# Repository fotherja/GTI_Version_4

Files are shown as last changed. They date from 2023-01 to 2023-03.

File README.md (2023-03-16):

# GTI_Version_4
This repo contains the hardware and software files for GTIv4. This is being superseded by GTIv5 (https://github.com/fotherja/Grid_Tie_Inverter_V5)

Hardware:
KiCad was used to design the 4-Layer PCB. This was manufactured by <a href="https://www.pcbway.com/">PCBWay</a> (They produce good quality PCBs for competitive prices with excellent turnaround times).

The board uses gallium nitride MASTERGAN2s and an isolated driver chip. Four AMC1306 isolated current shunt modulators read the various analogue signals and an STM32L475 powers the board.    

Problems: 1) The EMC filter capacitors are incorrectly connected up. It may reduce the performance of the EMI filtering. 2) On testing, at about 300 Watts one of the MASTERGAN2s exploded. The exact reason is unclear and so this hardware has been redesigned into V5.

Software:
Software was developed in STM32CubeIDE. We got as far as implementing a PR controller which was extremely working well. Needs lots more work though.

Problems: I did not manage to get the DFSDM analogue watchdog feature working to provide protection in case of overcurrent or overvoltage. I asked the question on StackOverflow but got no answers (https://stackoverflow.com/questions/75287992/cant-get-the-analogue-watchdog-to-trigger-an-interrupt-on-the-dfsdm-peripheral)

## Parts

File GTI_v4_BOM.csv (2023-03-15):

Ref | Qnty | Value | Footprint | Link to Part
C1, C2, C3, C4, C10, C18, C19, C35, C39, C42, C43, C45, C48, C51, C52, C57, C60, C62, C63, C65, C68, C69, C70, | 23 | 100nF | Capacitor_SMD:C_0603_1608Metric
C5, C21, | 2 | 0.47uF | Capacitor_SMD:C_2225_5664Metric
C6, C14, C23, C26, C32, | 5 | 47nF | Capacitor_SMD:C_0402_1005Metric
C7, C8, C24, C38, C41, C47, C56, C59, C64, C67, C71, | 11 | 1uF | Capacitor_SMD:C_0603_1608Metric
C9, | 1 | 47uF | Capacitor_SMD:C_0402_1005Metric
C11, C25, C29, | 3 | 4.7uF | Capacitor_SMD:C_0603_1608Metric
C12, C13, C30, C31, | 4 | 22pF | Capacitor_SMD:C_0603_1608Metric
C15, C33, | 2 | 330pF | Capacitor_SMD:C_0603_1608Metric
C16, C17, | 2 | 20pF | Capacitor_SMD:C_0603_1608Metric
C20, | 1 | 1uF | Capacitor_THT:C_Rect_L27.0mm_W11.0mm_P22.00mm | https://www.digikey.co.uk/en/products/detail/epcos-tdk-electronics/B32672Z4105K000/1648137?so=79236903
C22, C27, C28, | 3 | 2200pF | C901U222MZVDBA7317:C901U222MZVDBA7317 | https://www.mouser.co.uk/ProductDetail/KEMET/C901U222MZVDBA7317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
C34, C49, C50, | 3 | 22uF | 595D226X9020:CAPPC3328X220N | https://www.mouser.co.uk/ProductDetail/Vishay-Sprague/595D226X9020B2T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
C36, C53, C61, | 3 | 100pF | Capacitor_SMD:C_0603_1608Metric
C37, C54, C55, | 3 | 2.2uF | Capacitor_SMD:C_0603_1608Metric
C40, C46, C58, C66, | 4 | 10nF | Capacitor_SMD:C_0603_1608Metric
C44, | 1 | 0.47uF | Capacitor_THT:C_Rect_L31.5mm_W17.0mm_P27.50mm_MKS4 | https://www.mouser.co.uk/ProductDetail/Vishay-Roederstein/MKP1848610454K2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
C73, | 1 | 10uF | Capacitor_SMD:C_0805_2012Metric
C74, C75, | 2 | 10uF | Capacitor_SMD:C_0603_1608Metric
D1, D2, D3, | 3 | SB05W05C-TB-E | SB05W05C:SOT95P250X135-3N | https://www.mouser.co.uk/ProductDetail/onsemi/SB05W05C-TB-E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
D4, | 1 | LED | LED_SMD:LED_0603_1608Metric
D6, | 1 | DIODE | ES1J:DIOM5227X250N
H1, H2, H3, H4, | 4 | MountingHole | MountingHole:MountingHole_3.2mm_M3
IC1, IC2, | 2 | MASTERGAN2TR | MASTERGAN2:MASTERGAN2TR | https://www.mouser.co.uk/ProductDetail/STMicroelectronics/MASTERGAN2TR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
IC3, IC7, IC8, | 3 | MAX253CSA+ | MAX253CSA:SOIC127P600X175-8N | https://www.mouser.co.uk/ProductDetail/Maxim-Integrated/MAX253CSA+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
IC4, IC5, IC6, IC9, | 4 | AMC1306M25QDWVRQ1 | AMC1306:SOIC127P1150X280-8N | https://www.mouser.co.uk/ProductDetail/Texas-Instruments/AMC1306M25QDWVRQ1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
J1, | 1 | Screw_Terminal_01x03 | TerminalBlock:TerminalBlock_bornier-3_P5.08mm
J2, J3, | 2 | Screw_Terminal_01x02 | TerminalBlock:TerminalBlock_bornier-2_P5.08mm
J4, | 1 | Conn_01x06_Male | Connector_PinHeader_1.27mm:PinHeader_1x06_P1.27mm_Vertical
JP1, | 1 | SolderJumper_3_Open | Jumper:SolderJumper-3_P1.3mm_Open_RoundedPad1.0x1.5mm
K1, K2, | 2 | G5LE-1 | Relay_THT:Relay_SPDT_Omron-G5LE-1 | https://www.mouser.co.uk/ProductDetail/Omron-Electronics/G5LE-1-VD-DC12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
L1, | 1 | 2mH | Inductor_THT:L_Toroid_Vertical_L35.1mm_W21.1mm_P18.50mm_Vishay_TJ6
L2, L4, | 2 | 470uH | Inductor_THT:L_Toroid_Vertical_L41.9mm_W19.1mm_P15.80mm_Vishay_TJ7
L3, | 1 | 744822301 | 744822301:WE-CMB_S5 | https://www.mouser.co.uk/ProductDetail/Wurth-Elektronik/744822301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
PS1, PS2, PS3, | 3 | AP2210K-5.0TRG1 | AP2210K-5.0TRG1:SOT95P282X130-5N | https://www.mouser.co.uk/ProductDetail/Diodes-Incorporated/AP2210K-5.0TRG1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
Q2, | 1 | 2N7002 | Package_TO_SOT_SMD:SOT-23
R1, R6, R16, R17, R18, R19, R21, R22, R23, R28, | 10 | 10R | Resistor_SMD:R_0603_1608Metric
R2, R4, R11, R15, | 4 | 47R | Resistor_SMD:R_0603_1608Metric
R3, R12, R13, R20, R27, R29, R30, | 7 | 1K | Resistor_SMD:R_0603_1608Metric
R5, R8, R9, R24, R25, R26, | 6 | 470K | Resistor_SMD:R_0805_2012Metric
R7, | 1 | 6.8R | Resistor_SMD:R_2512_6332Metric | https://www.digikey.co.uk/en/products/detail/yageo/AC2512FK-076R8L/5899890?so=79236903
R10, R14, | 2 | 50mR | Resistor_SMD:R_2512_6332Metric
T1, T2, T3, | 3 | 760390014 | 760390014:760390015 | https://www.mouser.co.uk/ProductDetail/Wurth-Elektronik/760390014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
U1, | 1 | STM32L475RCTx | Package_QFP:LQFP-64_10x10mm_P0.5mm | https://www.mouser.co.uk/ProductDetail/STMicroelectronics/STM32L475RCT3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
U2, | 1 | Si8640EC-B-IS1 | Package_SO:SOIC-16_3.9x9.9mm_P1.27mm | https://www.digikey.co.uk/en/products/detail/skyworks-solutions-inc/SI8640EC-B-IS1/2623332?so=79236903
U3, | 1 | AZ1117-5.0 | AZ1117CD-5.0TRG1:AZ1117CD50TRG1 | https://www.mouser.co.uk/ProductDetail/Diodes-Incorporated/AZ1117CD-5.0TRG1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
U4, | 1 | NCP1117-3.3_SOT223 | Package_TO_SOT_SMD:SOT-223-3_TabPin2
Y1, | 1 | ABM10-16.000MHZ-D30-T3 | Crystal:Crystal_SMD_Abracon_ABM10-4Pin_2.5x2.0mm | https://www.mouser.co.uk/ProductDetail/ABRACON/ABM10-16.000MHZ-D30-T3?qs=yJy3i4hRrMhOYZI5v9%2F5mA%3D%3D

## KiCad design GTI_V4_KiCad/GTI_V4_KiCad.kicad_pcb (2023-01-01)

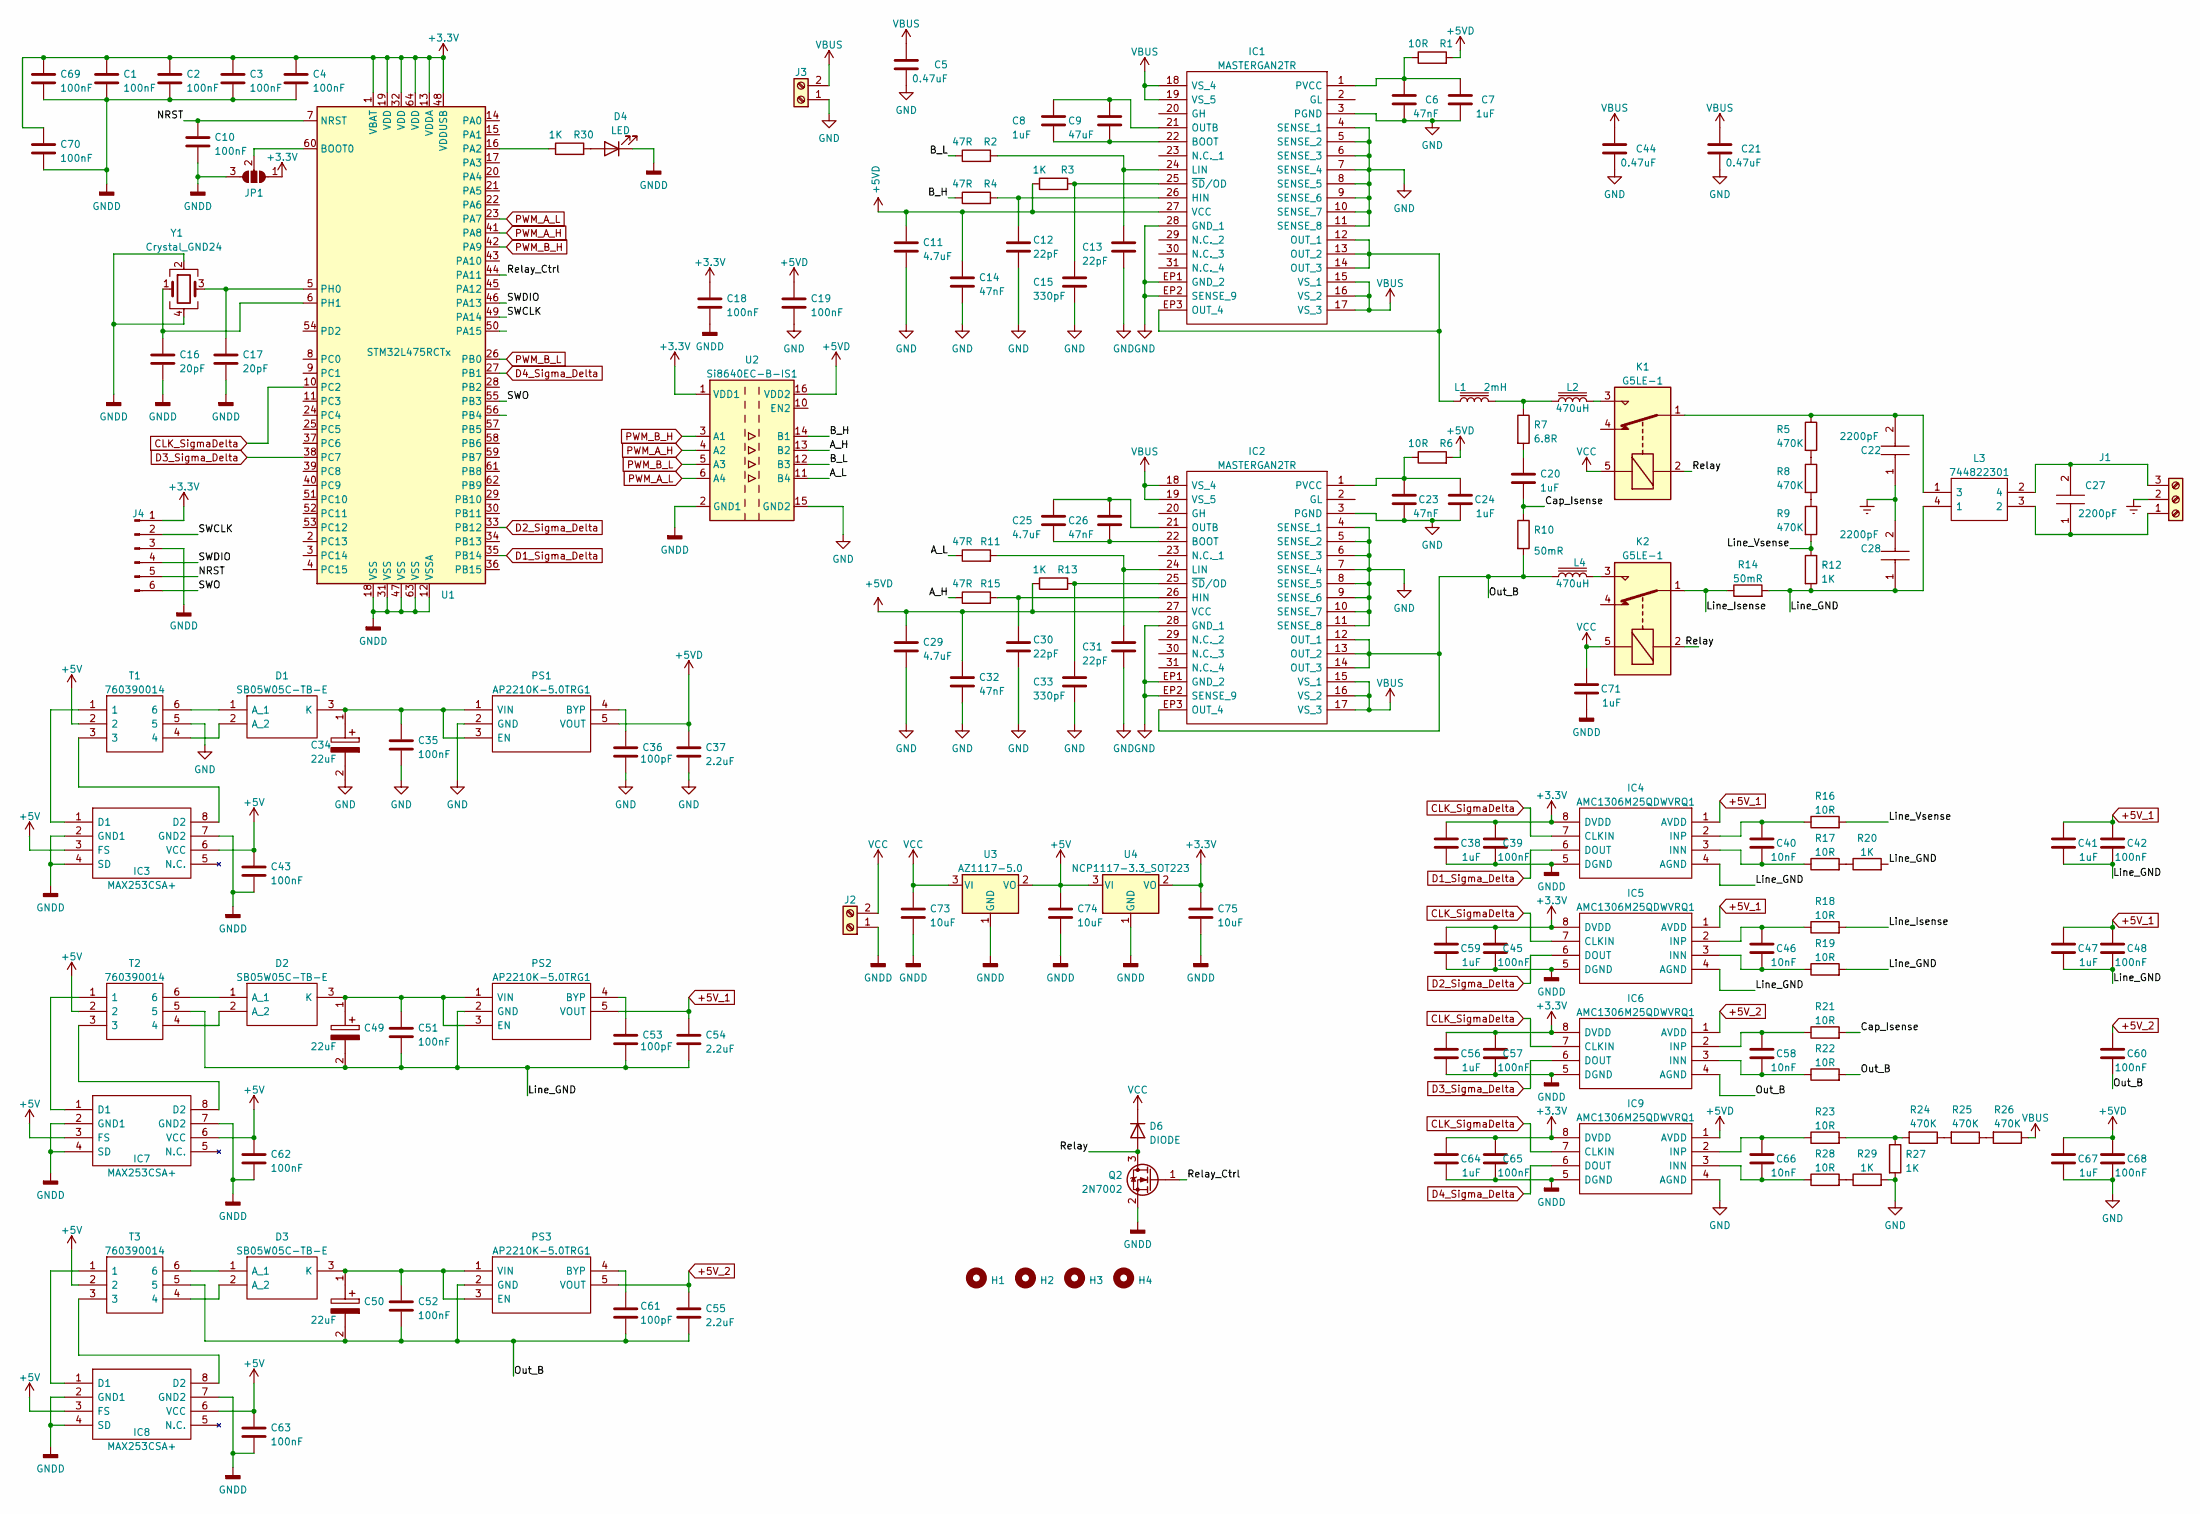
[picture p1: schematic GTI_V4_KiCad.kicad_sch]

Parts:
C1, C2, C3, C4, C10, C18, C19, C35, C39, C42, C43, C45, C48, C51, C52, C57, C60, C62, C63, C65, C68, C69, C70: 100nF; C_0603_1608Metric
C5, C21: 0.47uF; C_2225_5664Metric
C6, C14, C23, C26, C32: 47nF; C_0402_1005Metric
C7, C8, C24, C38, C41, C47, C56, C59, C64, C67, C71: 1uF; C_0603_1608Metric
C9: 47uF; C_0402_1005Metric
C11, C25, C29: 4.7uF; C_0603_1608Metric
C12, C13, C30, C31: 22pF; C_0603_1608Metric
C15, C33: 330pF; C_0603_1608Metric
C16, C17: 20pF; C_0603_1608Metric
C20: 1uF; C_Rect_L27.0mm_W11.0mm_P22.00mm
C22, C27, C28: 2200pF; C901U222MZVDBA7317; Mouser Part Number 80-C901U222MZVDBAP
C34, C49, C50: 22uF; CAPPC3328X220N; Mouser Part Number 74-595D226X9020B2T
C36, C53, C61: 100pF; C_0603_1608Metric
C37, C54, C55: 2.2uF; C_0603_1608Metric
C40, C46, C58, C66: 10nF; C_0603_1608Metric
C44: 0.47uF; C_Rect_L31.5mm_W17.0mm_P27.50mm_MKS4
C73: 10uF; C_0805_2012Metric
C74, C75: 10uF; C_0603_1608Metric
D1, D2, D3: SB05W05C-TB-E; SOT95P250X135-3N; Mouser Part Number 863-SB05W05C-TB-E
D4: LED; LED_0603_1608Metric
D6: DIODE; DIOM5227X250N
H1, H2, H3, H4: MountingHole; MountingHole_3.2mm_M3
IC1, IC2: MASTERGAN2TR; Mouser Part Number 511-MASTERGAN2TR
IC3, IC7, IC8: MAX253CSA+; SOIC127P600X175-8N; Mouser Part Number 700-MAX253CSA
IC4, IC5, IC6, IC9: AMC1306M25QDWVRQ1; SOIC127P1150X280-8N; Mouser Part Number 595-MC1306M25QDWVRQ1
J1: Screw_Terminal_01x03; TerminalBlock_bornier-3_P5.08mm
J2, J3: Screw_Terminal_01x02; TerminalBlock_bornier-2_P5.08mm
J4: Conn_01x06_Male; PinHeader_1x06_P1.27mm_Vertical
JP1: SolderJumper_3_Open; SolderJumper-3_P1.3mm_Open_RoundedPad1.0x1.5mm
K1, K2: G5LE-1; Relay_SPDT_Omron-G5LE-1
L1: 2mH; L_Toroid_Vertical_L35.1mm_W21.1mm_P18.50mm_Vishay_TJ6
L2, L4: 470uH; L_Toroid_Vertical_L41.9mm_W19.1mm_P15.80mm_Vishay_TJ7
L3: 744822301; WE-CMB_S5; Mouser Part Number 710-744822301
PS1, PS2, PS3: AP2210K-5.0TRG1; SOT95P282X130-5N; Mouser Part Number 621-AP2210K-5.0TRG1
Q2: 2N7002; SOT-23
R1, R6, R16, R17, R18, R19, R21, R22, R23, R28: 10R; R_0603_1608Metric
R2, R4, R11, R15: 47R; R_0603_1608Metric
R3, R12, R13, R20, R27, R29, R30: 1K; R_0603_1608Metric
R5, R8, R9, R24, R25, R26: 470K; R_0805_2012Metric
R7: 6.8R; R_2512_6332Metric
R10, R14: 50mR; R_2512_6332Metric
T1, T2, T3: 760390014; 760390015; Mouser Part Number 710-760390014
U1: STM32L475RCTx; LQFP-64_10x10mm_P0.5mm
U2: Si8640EC-B-IS1; SOIC-16_3.9x9.9mm_P1.27mm
U3: AZ1117-5.0; AZ1117CD50TRG1
U4: NCP1117-3.3_SOT223; SOT-223-3_TabPin2
Y1: Crystal_GND24; Crystal_SMD_Abracon_ABM10-4Pin_2.5x2.0mm

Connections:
+3.3V: C1.1, C2.1, C3.1, C4.1, C18.1, C38.1, C39.1, C45.1, C56.1, C57.1, C59.1, C64.1, C65.1, C69.1, C70.1, C75.1, IC4.8 (DVDD), IC5.8 (DVDD), IC6.8 (DVDD), IC9.8 (DVDD), J4.1, JP1.1 (A), U1.1 (VBAT), U1.13 (VDDA), U1.19 (VDD), U1.32 (VDD), U1.48 (VDDUSB), U1.64 (VDD), U2.1 (VDD1), U4.2 (VO)
+5V: C43.1, C62.1, C63.1, C74.1, IC3.3 (FS), IC3.6 (VCC), IC7.3 (FS), IC7.6 (VCC), IC8.3 (FS), IC8.6 (VCC), T1.2, T2.2, T3.2, U3.2 (VO), U4.3 (VI)
+5VD: C11.1, C14.1, C19.1, C29.1, C32.1, C37.1, C67.1, C68.1, IC1.27 (VCC), IC2.27 (VCC), IC9.1 (AVDD), PS1.5 (VOUT), R1.2, R3.1, R6.2, R13.1, U2.16 (VDD2)
+5V_1: C41.1, C42.1, C47.1, C48.1, C54.1, IC4.1 (AVDD), IC5.1 (AVDD), PS2.5 (VOUT)
+5V_2: C55.1, C60.1, IC6.1 (AVDD), PS3.5 (VOUT)
/A_H: R15.1, U2.13 (B2)
/A_L: R11.1, U2.11 (B4)
/B_H: R4.1, U2.14 (B1)
/B_L: R2.1, U2.12 (B3)
/Cap_Isense: C20.2, R10.1, R21.2
/Line_GND: C28.1, C41.2, C42.2, C47.2, C48.2, C49.2, C51.2, C53.2, C54.2, IC4.4 (AGND), IC5.4 (AGND), L3.4 (1), PS2.2 (GND), R12.2, R14.2, R19.2, R20.2, T2.5
/Line_Isense: K2.1, R14.1, R18.2
/Line_Vsense: R9.2, R12.1, R16.2
/NRST: C10.1, J4.5, U1.7 (NRST)
/Out_B: C50.2, C52.2, C55.2, C60.2, C61.2, IC2.12 (OUT_1), IC2.13 (OUT_2), IC2.14 (OUT_3), IC2.EP3 (OUT_4), IC6.4 (AGND), L4.1, PS3.2 (GND), R10.2, R22.2, T3.5
/Relay: D6.1 (A), K1.2, K2.2, Q2.3 (D)
/Relay_Ctrl: Q2.1 (G), U1.44 (PA11)
/SWCLK: J4.2, U1.49 (PA14)
/SWDIO: J4.4, U1.46 (PA13)
/SWO: J4.6, U1.55 (PB3)
CLK_SigmaDelta: IC4.7 (CLKIN), IC5.7 (CLKIN), IC6.7 (CLKIN), IC9.7 (CLKIN), U1.10 (PC2)
D1_Sigma_Delta: IC4.6 (DOUT), U1.35 (PB14)
D2_Sigma_Delta: IC5.6 (DOUT), U1.33 (PB12)
D3_Sigma_Delta: IC6.6 (DOUT), U1.38 (PC7)
D4_Sigma_Delta: IC9.6 (DOUT), U1.27 (PB1)
Earth: C22.1, C28.2, J1.2
GND: C5.2, C6.2, C7.2, C11.2, C12.2, C13.2, C14.2, C15.2, C19.2, C21.2, C23.2, C24.2, C29.2, C30.2, C31.2, C32.2, C33.2, C34.2, C35.2, C36.2, C37.2, C44.2, C67.2, C68.2, IC1.3 (PGND), IC1.4 (SENSE_1), IC1.5 (SENSE_2), IC1.6 (SENSE_3), IC1.7 (SENSE_4), IC1.8 (SENSE_5), IC1.9 (SENSE_6), IC1.10 (SENSE_7), IC1.11 (SENSE_8), IC1.28 (GND_1), IC1.EP1 (GND_2), IC1.EP2 (SENSE_9), IC2.3 (PGND), IC2.4 (SENSE_1), IC2.5 (SENSE_2), IC2.6 (SENSE_3), IC2.7 (SENSE_4), IC2.8 (SENSE_5), IC2.9 (SENSE_6), IC2.10 (SENSE_7), IC2.11 (SENSE_8), IC2.28 (GND_1), IC2.EP1 (GND_2), IC2.EP2 (SENSE_9), IC9.4 (AGND), J3.1, PS1.2 (GND), R27.2, R29.2, T1.5, U2.9 (GND2), U2.15 (GND2)
GNDD: C1.2, C2.2, C3.2, C4.2, C10.2, C16.2, C17.2, C18.2, C38.2, C39.2, C43.2, C45.2, C56.2, C57.2, C59.2, C62.2, C63.2, C64.2, C65.2, C69.2, C70.2, C71.2, C73.2, C74.2, C75.2, D4.1 (K), IC3.2 (GND1), IC3.4 (SD), IC3.7 (GND2), IC4.5 (DGND), IC5.5 (DGND), IC6.5 (DGND), IC7.2 (GND1), IC7.4 (SD), IC7.7 (GND2), IC8.2 (GND1), IC8.4 (SD), IC8.7 (GND2), IC9.5 (DGND), J2.1, J4.3, JP1.3 (B), Q2.2 (S), U1.12 (VSSA), U1.18 (VSS), U1.31 (VSS), U1.47 (VSS), U1.63 (VSS), U2.2 (GND1), U2.8 (GND1), U3.1 (GND), U4.1 (GND), Y1.2, Y1.4
unnamed: C6.1, C7.1, IC1.1 (PVCC), R1.1
unnamed: C8.1, C9.1, IC1.21 (OUTB)
unnamed: C8.2, C9.2, IC1.22 (BOOT)
unnamed: C12.1, IC1.26 (HIN), R4.2
unnamed: C13.1, IC1.24 (LIN), R2.2
unnamed: C15.1, IC1.25 (~SD/OD), R3.2
unnamed: C16.1, U1.6 (PH1), Y1.1
unnamed: C17.1, U1.5 (PH0), Y1.3
unnamed: C20.1, R7.2
unnamed: C22.2, K1.1, L3.1 (3), R5.1
unnamed: C23.1, C24.1, IC2.1 (PVCC), R6.1
unnamed: C25.1, C26.1, IC2.21 (OUTB)
unnamed: C25.2, C26.2, IC2.22 (BOOT)
unnamed: C27.1, J1.1, L3.3 (2)
unnamed: C27.2, J1.3, L3.2 (4)
unnamed: C30.1, IC2.26 (HIN), R15.2
unnamed: C31.1, IC2.24 (LIN), R11.2
unnamed: C33.1, IC2.25 (~SD/OD), R13.2
unnamed: C34.1, C35.1, D1.3 (K), PS1.1 (VIN), PS1.3 (EN)
unnamed: C36.1, PS1.4 (BYP)
unnamed: C40.1, IC4.2 (INP), R16.1
unnamed: C40.2, IC4.3 (INN), R17.1
unnamed: C46.1, IC5.2 (INP), R18.1
unnamed: C46.2, IC5.3 (INN), R19.1
unnamed: C49.1, C51.1, D2.3 (K), PS2.1 (VIN), PS2.3 (EN)
unnamed: C50.1, C52.1, D3.3 (K), PS3.1 (VIN), PS3.3 (EN)
unnamed: C53.1, PS2.4 (BYP)
unnamed: C58.1, IC6.2 (INP), R21.1
unnamed: C58.2, IC6.3 (INN), R22.1
unnamed: C61.1, PS3.4 (BYP)
unnamed: C66.1, IC9.2 (INP), R23.1
unnamed: C66.2, IC9.3 (INN), R28.1
unnamed: D1.1 (A_1), T1.6
unnamed: D1.2 (A_2), T1.4
unnamed: D2.1 (A_1), T2.6
unnamed: D2.2 (A_2), T2.4
unnamed: D3.1 (A_1), T3.6
unnamed: D3.2 (A_2), T3.4
unnamed: D4.2 (A), R30.2
unnamed: IC1.12 (OUT_1), IC1.13 (OUT_2), IC1.14 (OUT_3), IC1.EP3 (OUT_4), L1.1
unnamed: IC3.1 (D1), T1.1
unnamed: IC3.8 (D2), T1.3
unnamed: IC7.1 (D1), T2.1
unnamed: IC7.8 (D2), T2.3
unnamed: IC8.1 (D1), T3.1
unnamed: IC8.8 (D2), T3.3
unnamed: JP1.2 (C), U1.60 (BOOT0)
unnamed: K1.3, L2.2
unnamed: K2.3, L4.2
unnamed: L1.2, L2.1, R7.1
unnamed: R5.2, R8.1
unnamed: R8.2, R9.1
unnamed: R17.2, R20.1
unnamed: R23.2, R24.2, R27.1
unnamed: R24.1, R25.2
unnamed: R25.1, R26.2
unnamed: R28.2, R29.1
unnamed: R30.1, U1.16 (PA2)
PWM_A_H: U1.41 (PA8), U2.4 (A2)
PWM_A_L: U1.23 (PA7), U2.6 (A4)
PWM_B_H: U1.42 (PA9), U2.3 (A1)
PWM_B_L: U1.26 (PB0), U2.5 (A3)
VBUS: C5.1, C21.1, C44.1, IC1.15 (VS_1), IC1.16 (VS_2), IC1.17 (VS_3), IC1.18 (VS_4), IC1.19 (VS_5), IC2.15 (VS_1), IC2.16 (VS_2), IC2.17 (VS_3), IC2.18 (VS_4), IC2.19 (VS_5), J3.2, R26.1
VCC: C71.1, C73.1, D6.2 (K), J2.2, K1.5, K2.5, U3.3 (VI)

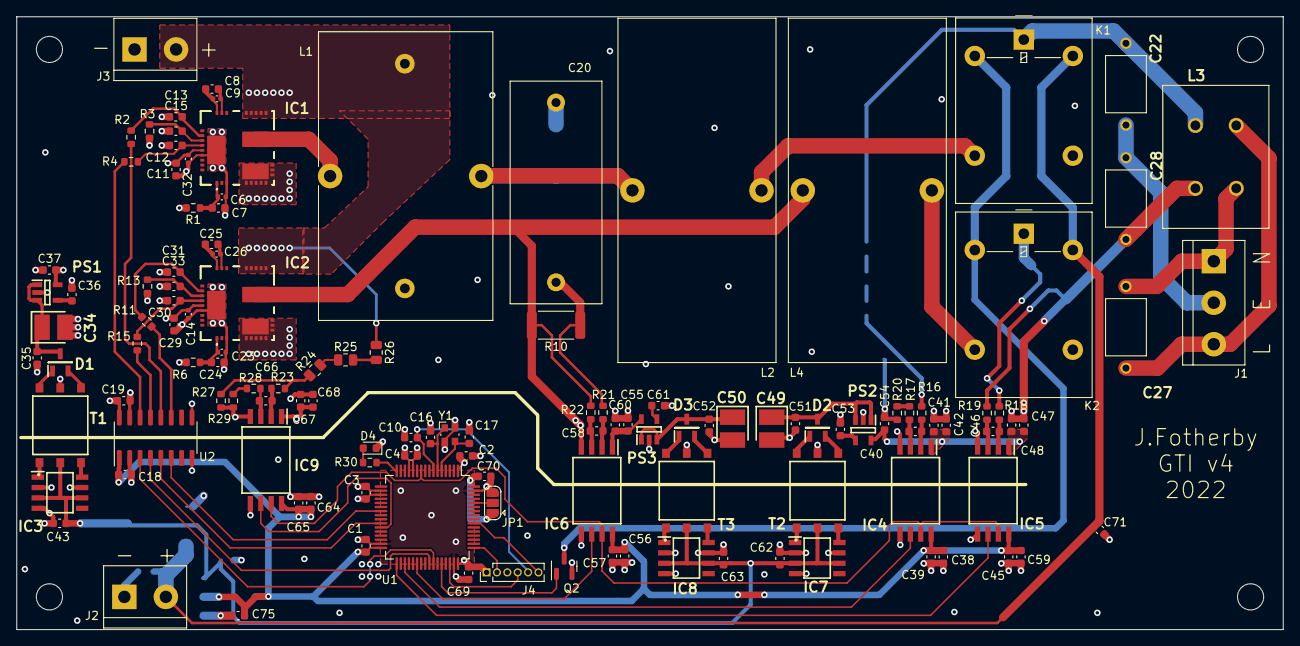
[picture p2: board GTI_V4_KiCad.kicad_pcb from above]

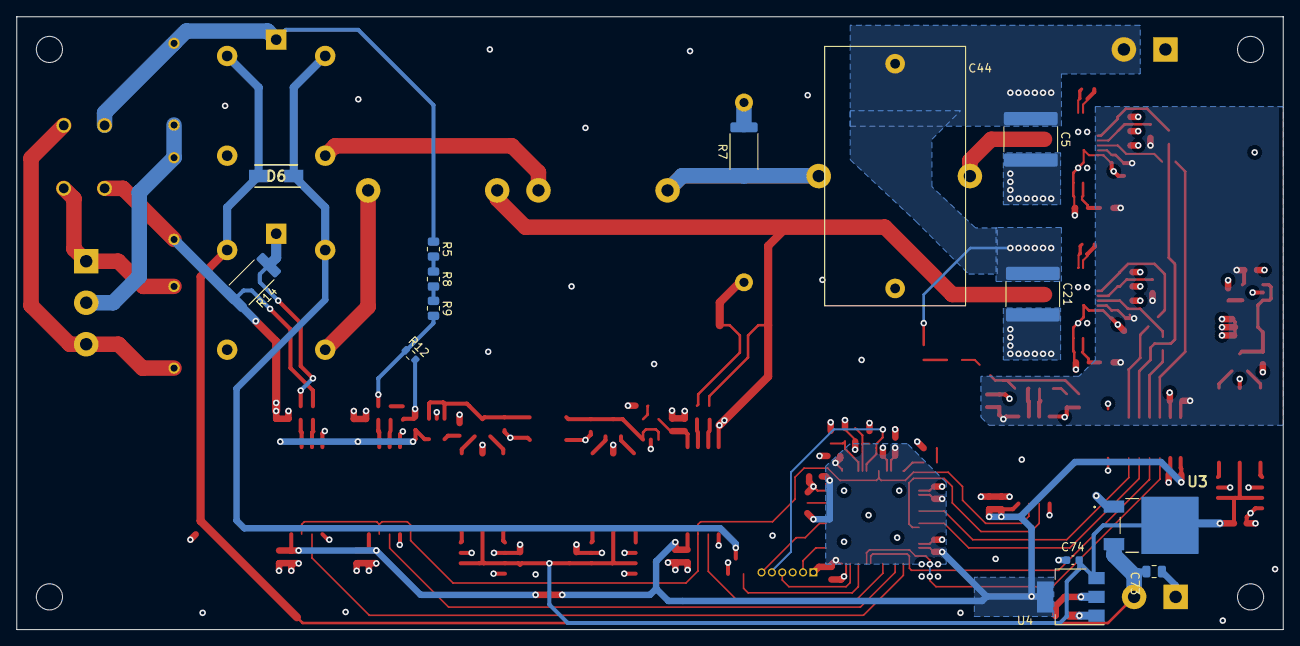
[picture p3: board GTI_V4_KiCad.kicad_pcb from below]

Board: 4 copper layers, 155.0 x 75.0 mm, 145 parts (14 on the bottom side), 92 nets.

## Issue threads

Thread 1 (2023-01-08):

Hi

Jmenotts, 2023-01-08:
My name is James i'm new to this and ive downloaded your files but cant seem to get the code for the stm32 chip but isnt in the download folder? also will this work on an esp32 by any chance i'm trying to build a grid tie inverter so i can save some electric thanks in advance buddy.

fotherja, 2023-01-08:
Hi, GTI_Version 4 is a work in progress. In this repo are just the PCB design files atm. I'm waiting for the PCB board to be posted (due 10th Jan).
Once I receive the PCB I need to assemble it and adapt/improve the software.
With version 4 I want to implement a PR controller.

Jmenotts, 2023-01-08:
Hi and thank you for your email buddy your work is incredible tbh and I'm
following extensively do you have working code I can play with on any
version you have? I'm dying to get into this field and have a play with
this renewable energy stuff it's very intriguing. Thanks in advance

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

fotherja, 2023-01-08:
Thanks. I think the code I've been using for the previous versions needs a total overhaul. Here are some useful resources:
Poldo on instructables: https://www.instructables.com/search/projects/?q=poldo&projects=all
PR controllers and how to implement them: https://imperix.com/doc/implementation/proportional-resonant-controller

Watch this space. Hope in the next month to get version 4 made.

Jmenotts, 2023-01-08:
Awesome, thanks! Will look forward to the update buddy

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

Flole998, 2023-02-09:
I'm also looking into building a grid tie inverter. At this point I am doing hardware design since I am trying to avoid using transformers. I'm trying to use a charge pump  for step-up conversion and I will shortly have the first revision of my PCB produced. Since the H-Bridge and filters are similar in our designs I believe we can learn a lot from each other when it comes to the software.

fotherja, 2023-02-15:
Hi,
I'm very interested to hear more. How are you planning to use a charge pump
for hundreds of watts? Can I see your PCB designs?

I'm writing up my 4th attempt and will post it soon. I have managed to
implement a PR controller very well. I was very pleased with my hardware
for my 4th attempt. Everything was going extremely well until a MOSFET
package blew up a couple days ago... So now I think I need to look into a
5th version and some hardware changes.

Yes I'd be very keen to collaborate with the code. What microprocessor are
you using? Stay in touch. my email is ***@***.***

James

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

Flole998, 2023-02-15:
Hi James,

unfortunately GitHub censored your email address :D

My idea is to use the design from https://onlinelibrary.wiley.com/cms/asset/b8836dac-32ef-46b6-ad67-28f952f7738e/etep12622-toc-0001-m.jpg which was tested at 150W and converted 18V into 350V, as it's basically doing multiplication of the input voltage at 36V I could already get 700V out of it if I'm not mistaken, increasing the current should pull the voltage down and also increase output power.

I'm using an Attiny3226 for the boost converter (and MPTT, measuring input voltage and current) and an AVR128DB32 for the H bridge, measuring zero cross, output voltage and current and communication with a CAN bus (I use that for my building automation).

fotherja, 2023-02-21:
Hey,

Interesting. Well keep me updated with your progress. I have a gmail
address. And prior to the @ sign is the same as my github username...

I have just posted my version 4 attempt.
https://www.instructables.com/Grid-Tie-Inverter-V4/

James

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

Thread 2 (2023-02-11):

CT Current limiting

folny, 2023-02-11:
Hi

I like your project and I'm already very curious about the first tests, I want to ask if in the future you plan to add an input for the CT sensor to the project to prevent the flow of current into the distributor network.

https://www.aliexpress.com/item/1005004501300085.html

fotherja, 2023-02-15:
Hi,
Thanks. I'm writing up my 4th attempt and will post it soon. Unfortunately,
I'll need a 5th attempt. The 4th version was going extremely well until it
blew up...
Yes, a CT sensor will be very useful in future.
James

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

folny, 2023-02-17:
I'm keeping my fingers crossed and I'll be watching your project and I hope you'll soon figure out how to bring it to perfection :-)

fotherja, 2023-02-21:
Hey,

I have just posted my version 4 attempt.
https://www.instructables.com/Grid-Tie-Inverter-V4/

Already thinking about version 5. If you have any recommendations, I'd be
glad to hear them.

James

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

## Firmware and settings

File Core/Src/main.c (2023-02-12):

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
/* Includes ------------------------------------------------------------------*/
#include "main.h"
#include "dac.h"
#include "dfsdm.h"
#include "dma.h"
#include "tim.h"
#include "gpio.h"

/* USER CODE BEGIN Includes */
#include "PID.h"
#include "math.h"
/* USER CODE END Includes */


/* USER CODE BEGIN PV */
float Sin_LookupF[65] =
{
		0, 25.09238792, 49.94312244, 74.31287738, 97.96695869, 120.6775646, 142.2259797, 162.4046807,
		181.019336, 197.8906761, 212.8562207, 225.7718437, 236.5131603, 244.9767259, 251.0810318, 254.76729,
		256, 254.76729, 251.0810318, 244.9767259, 236.5131603, 225.7718437, 212.8562207, 197.8906761,
		181.019336,	162.4046807, 142.2259797, 120.6775646, 97.96695869, 74.31287738, 49.94312244, 25.09238792,
		0, -25.09238792, -49.94312244, -74.31287738, -97.96695869, -120.6775646, -142.2259797, -162.4046807,
		-181.019336, -197.8906761, -212.8562207, -225.7718437, -236.5131603, -244.9767259, -251.0810318, -254.76729,
		-256, -254.76729, -251.0810318, -244.9767259, -236.5131603, -225.7718437, -212.8562207, -197.8906761,
		-181.019336, -162.4046807, -142.2259797, -120.6775646, -97.96695869, -74.31287738, -49.94312244, -25.09238792,
		0
};

float Cos_LookupF[65] =
{
		256, 254.76729, 251.0810318, 244.9767259, 236.5131603, 225.7718437, 212.8562207, 197.8906761,
		181.019336, 162.4046807, 142.2259797, 120.6775646, 97.96695869, 74.31287738, 49.94312244, 25.09238792,
		0, -25.09238792, -49.94312244, -74.31287738, -97.96695869, -120.6775646, -142.2259797, -162.4046807,
		-181.019336, -197.8906761, -212.8562207, -225.7718437, -236.5131603, -244.9767259, -251.0810318, -254.76729,
		-256, -254.76729, -251.0810318, -244.9767259, -236.5131603, -225.7718437, -212.8562207, -197.8906761,
		-181.019336, -162.4046807, -142.2259797, -120.6775646, -97.96695869, -74.31287738, -49.94312244, -25.09238792,
		0, 25.09238792, 49.94312244, 74.31287738, 97.96695869, 120.6775646, 142.2259797, 162.4046807,
		181.019336,	197.8906761, 212.8562207, 225.7718437, 236.5131603, 244.9767259, 251.0810318, 254.76729,
		256
};

// PID Structures
PIDControl 			PLL_PID, I_OUT_PID; 										// These structures are used to store the respective PID variables

// DMA buffers and flags
int32_t 			Vbus_DMA[1], Igrid_DMA[1], Vgrid_DMA[1], Icap_DMA[1];
uint32_t			Channel_1_DUTY[1], Channel_2_DUTY[1];

// Voltage and Current values
float 				I_grid, V_grid, I_cap, V_bus; 								// These are our SI unit values

// LO Phase
uint8_t 			_50_Index = 0;

volatile uint8_t 	Error_Code;
volatile float 		I_Output_Demand = 0;

volatile uint8_t    Run_Controller_Flag = 0;
volatile uint8_t	Run_Grid_Checks_Flag = 0;
volatile uint8_t	Run_PLL_Flag = 0;
uint8_t				HB_Enabled_Flag = false;

/* USER CODE END PV */

void SystemClock_Config(void);
/* USER CODE BEGIN PFP */
void HB_Disable(void);
void HB_Enable(void);
float Integral(int32_t datum);
void Grid_Checks(void);
void Controller(void);
void PLL(void);
void Main_Loop(void);
int32_t Integrate_Mains_MS(int32_t grid_voltage_sample);
void HAL_DFSDM_FilterAwdCallback(DFSDM_Filter_HandleTypeDef *hdfsdm_filter, uint32_t Channel, uint32_t Threshold);
void HAL_DFSDM_FilterRegConvCpltCallback(DFSDM_Filter_HandleTypeDef *hdfsdm_filter);
/* USER CODE END PFP */

/**
  * @brief  The application entry point.
  * @retval int
  */
int main(void)
{
  /* MCU Configuration--------------------------------------------------------*/

  /* Reset of all peripherals, Initializes the Flash interface and the Systick. */
  HAL_Init();

  /* Configure the system clock */
  SystemClock_Config();

  /* Initialize all configured peripherals */
  MX_GPIO_Init();
  MX_DMA_Init();
  MX_TIM1_Init();
  MX_TIM3_Init();
  MX_DFSDM1_Init();
  MX_TIM2_Init();
  MX_TIM4_Init();
  MX_DAC1_Init();
  /* USER CODE BEGIN 2 */
  // Initialise the PID controller for the PLL
  PIDInit(&PLL_PID, PLL_Kp, PLL_Ki, PLL_Kd, PLL_PERIOD, -PLL_LIMIT, PLL_LIMIT, AUTOMATIC, DIRECT, P_ON_E);
  PIDInit(&I_OUT_PID, I_OUT_Kp, I_OUT_Ki, I_OUT_Kd, I_OUT_PERIOD, -I_OUT_Limit, I_OUT_Limit, AUTOMATIC, DIRECT, P_ON_E);

  // Initialise our timers
  HAL_TIM_Base_Start_IT(&htim2);
  HAL_TIM_Base_Start_IT(&htim3);
  HAL_TIM_Base_Start_IT(&htim4);

  // Initialise DAC and LED for Debugging
  HAL_DAC_Start(&hdac1, DAC_CHANNEL_2);
  HAL_GPIO_WritePin(GPIOA, Relay_Pin, GPIO_PIN_SET);

  // Start the DFSDMs
  HAL_DFSDM_FilterRegularStart_DMA(&hdfsdm1_filter0, Vbus_DMA, 1);
  HAL_DFSDM_FilterRegularStart_DMA(&hdfsdm1_filter1, Igrid_DMA, 1);
  HAL_DFSDM_FilterRegularStart_DMA(&hdfsdm1_filter2, Vgrid_DMA, 1);
  HAL_DFSDM_FilterRegularStart_DMA(&hdfsdm1_filter3, Icap_DMA, 1);

  // This should enable the interrupts by the analogue watchdog ----------- BUT IT DOESN'T!!!
  DFSDM_Filter_AwdParamTypeDef awdParamFilter0;
  awdParamFilter0.DataSource = DFSDM_FILTER_AWD_FILTER_DATA;
  awdParamFilter0.Channel = DFSDM_CHANNEL_0;
  awdParamFilter0.HighBreakSignal = DFSDM_NO_BREAK_SIGNAL;
  awdParamFilter0.HighThreshold = 250;
  awdParamFilter0.LowBreakSignal = DFSDM_NO_BREAK_SIGNAL;
  awdParamFilter0.LowThreshold = -250;
  HAL_DFSDM_FilterAwdStart_IT(&hdfsdm1_filter0, &awdParamFilter0);

  DFSDM_Filter_AwdParamTypeDef awdParamFilter1;
  awdParamFilter1.DataSource = DFSDM_FILTER_AWD_FILTER_DATA;
  awdParamFilter1.Channel = DFSDM_CHANNEL_1;
  awdParamFilter1.HighBreakSignal = DFSDM_NO_BREAK_SIGNAL;
  awdParamFilter1.HighThreshold = 250;
  awdParamFilter1.LowBreakSignal = DFSDM_NO_BREAK_SIGNAL;
  awdParamFilter1.LowThreshold = -250;
  HAL_DFSDM_FilterAwdStart_IT(&hdfsdm1_filter1, &awdParamFilter1);

  HAL_GPIO_WritePin(GPIOA, LED_Pin, GPIO_PIN_SET);
  /* USER CODE END 2 */

  /* Infinite loop */
  /* USER CODE BEGIN WHILE */

  while (1)
  {
    /* USER CODE END WHILE */

    /* USER CODE BEGIN 3 */
	  Main_Loop();
  }
  /* USER CODE END 3 */
}

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
/* USER CODE BEGIN 4 */
void Main_Loop()	{
	if(Run_Controller_Flag == 1)	{
		Run_Controller_Flag = 0;
		Controller();
	}

	if(Run_Grid_Checks_Flag == 1)	{
		Run_Grid_Checks_Flag = 0;
		Grid_Checks();
	}

	if(Run_PLL_Flag == 1)	{
		Run_PLL_Flag = 0;
		PLL();
	}
}

void HB_Disable() {
	// Disable the H-Bridge
	HAL_TIM_PWM_Stop(&htim1, TIM_CHANNEL_1);
	HAL_TIMEx_PWMN_Stop(&htim1, TIM_CHANNEL_1);
	HAL_TIM_PWM_Stop(&htim1, TIM_CHANNEL_2);
	HAL_TIMEx_PWMN_Stop(&htim1, TIM_CHANNEL_2);
	HB_Enabled_Flag = false;

	htim1.Instance->CCR1 = 0;
	htim1.Instance->CCR2 = 0;

	HAL_GPIO_WritePin(GPIOA, LED_Pin, GPIO_PIN_SET);
}

void HB_Enable() {
	// Start our PWM driver which uses Timer1 to power our H-bridge. Both channels start with Duty = 0
	HAL_GPIO_WritePin(GPIOA, LED_Pin, GPIO_PIN_RESET);

	HAL_TIM_PWM_Start(&htim1, TIM_CHANNEL_1);
	HAL_TIMEx_PWMN_Start(&htim1, TIM_CHANNEL_1);
	HAL_TIM_PWM_Start(&htim1, TIM_CHANNEL_2);
	HAL_TIMEx_PWMN_Start(&htim1, TIM_CHANNEL_2);
	HB_Enabled_Flag = true;
}

float Integral(int32_t datum)
{
	// Keep a running summation of the last INTEGRAL_SIZE values passed into this function.
	static int32_t 		Buffer[INTEGRAL_SIZE];
	static int16_t  	Index = 0;
	static int32_t  	Sum = 0;

	Sum += datum;

	Buffer[Index++] = datum;

	if(Index == INTEGRAL_SIZE)
		Index = 0;

	Sum -= Buffer[Index];
	return((float)Sum);
}

int32_t Integrate_Mains_MS(int32_t grid_voltage_sample)
{
	// Maintain an MS measurement of the grid voltage. Runs at 800Hz which is 16 samples per period
	static int32_t 		Buffer[RMS_INTEGRAL_SIZE];
	static int8_t  		Index = 0;
	static int32_t  	Sum = 0;

	int32_t Sample_sqrd = grid_voltage_sample * grid_voltage_sample;

	Sum += Sample_sqrd;

	Buffer[Index++] = Sample_sqrd;

	if(Index == RMS_INTEGRAL_SIZE)
		Index = 0;

	Sum -= Buffer[Index];

	int32_t Mean_Squared = Sum >> 6;			// Divide Sum by 64 (RMS_INTEGRAL_SIZE)
	return(Mean_Squared);						// return(sqrtf(RMS));
}

void HAL_DFSDM_FilterAwdCallback(DFSDM_Filter_HandleTypeDef *hdfsdm_filter, uint32_t Channel, uint32_t Threshold)
{
	// Callback if Analogue watch dog triggers ---------- BUT CAN'T GET THIS TO RUN!!!!
}

void HAL_DFSDM_FilterRegConvCpltCallback(DFSDM_Filter_HandleTypeDef *hdfsdm_filter)	{
	if(hdfsdm_filter == &hdfsdm1_filter0)	{
		V_bus = (float)Vbus_DMA[0] * 2.4414e-7 + 5.0e-4;
	}
	if(hdfsdm_filter == &hdfsdm1_filter1)	{
		I_grid = (float)Igrid_DMA[0] * -3.1738e-9 + 8.75e-6;
	}
	if(hdfsdm_filter == &hdfsdm1_filter2)	{
		V_grid = (float)Vgrid_DMA[0] * 2.4414e-7 + 5.0e-4;
	}
	if(hdfsdm_filter == &hdfsdm1_filter3)	{
		I_cap = (float)Icap_DMA[0] * 3.1738e-9 - 8.75e-6;
	}
}

void Grid_Checks()	{
	// Calculate some grid metrics for some following checks
	static int16_t 	Grid_Good_Bad_Cnt = GRID_UNACCEPTABLE;

	int32_t Mains_MS = Integrate_Mains_MS((int32_t)V_grid); 						// Update our mains RMS measurement
	float Freq_Offset = PLL_PID.output * F_CONVERSION_K; 							// Get the frequency difference between the grid and a 50Hz reference

	// These are high priority checks:
	if(V_bus > V_BUS_MAXIMUM)	{													// If our DC Bus voltage is too high cut-out immediately
		HB_Disable();
		Grid_Good_Bad_Cnt = GRID_UNACCEPTABLE;
		Error_Code |= 0b00001;
	}

	if(I_grid > I_OUTPUT_MAXIMUM || I_grid < -I_OUTPUT_MAXIMUM)	{					// Likewise, if we detect excess current flowing, cut-out immediately
		HB_Disable();
		Grid_Good_Bad_Cnt = GRID_UNACCEPTABLE;
		Error_Code |= 0b00010;
	}

	// These are lower priority checks and have to be out of range for an amount of time
	if(Mains_MS > RMS_UPPER_LIMIT || Mains_MS < RMS_LOWER_LIMIT)	{				// If mains RMS voltage whacky
		Grid_Good_Bad_Cnt -= GRID_BAD_FAIL_RATE;
		Error_Code |= 0b00100;
	}

	if(Freq_Offset > FREQ_DEVIATION_LIMIT || Freq_Offset < -FREQ_DEVIATION_LIMIT)	{
	//	Grid_Good_Bad_Cnt -= GRID_BAD_FAIL_RATE;									// If our mains frequency is out of tolerance
		Error_Code |= 0b01000;
	}

	if(V_bus < V_BUS_MINIMUM)	{													// If our DC Bus voltage is too low
		Grid_Good_Bad_Cnt -= GRID_BAD_FAIL_RATE;
		Error_Code |= 0b10000;
	}

	// Act on the above checks
	if(Grid_Good_Bad_Cnt < GRID_OK)	{												// If our metrics have been whacky for too long stop output
		if(HB_Enabled_Flag == true) {
			HB_Disable(); 															// This puts the H-bridge into a high impedance state
			Grid_Good_Bad_Cnt = GRID_UNACCEPTABLE;
		}
	}

	if(HB_Enabled_Flag == false) { 													// With our output idle, if the grid has normalised, restart
		if(Grid_Good_Bad_Cnt == GRID_ACCEPTABLE && ENABLE_JOINING_GRID == true) {
			HB_Enabled_Flag = REQUEST_JOIN_GRID;
			Error_Code = 0;
		}
	}

	// Constrain and decay any error counts
	Grid_Good_Bad_Cnt++;
	Grid_Good_Bad_Cnt = CONSTRAIN(Grid_Good_Bad_Cnt, GRID_UNACCEPTABLE, GRID_ACCEPTABLE);

	if(I_Output_Demand < 20.0e-3f)
		I_Output_Demand += 4.0e-6f;
}

void Controller()	{
	static int16_t Duty_Cycle;
	static int16_t Prev_Duty_Cycle;

	// This enables our H-Bridge at the up-going zero crossing point if we are requesting to join the grid.
	if(HB_Enabled_Flag == REQUEST_JOIN_GRID)	{
		if(_50_Index == 0)	{
			I_Output_Demand = 16.0e-4f;
			I_OUT_PID.iTerm = 0;
			HB_Enable();
		}
	}

	// Interpolate our LO steps to get a more accurate LO sample:
	uint32_t Timer4_CNT = TIM4->CNT;												// Take records of the current counter values
	uint8_t Lookup_Index = _50_Index;
	float diff = Sin_LookupF[Lookup_Index + 1] - Sin_LookupF[Lookup_Index];
	float Timer4_CNT_Ratio = 0.001f * (float)Timer4_CNT;
	float LO_Sample_256 = Sin_LookupF[Lookup_Index] + diff * Timer4_CNT_Ratio;

	// -------------- Iterate our PI+R Controller:
	 float const kr = 5000.0;
	 float const Wdamp_50 = 2.0 * 3.1415927 * 0.75;
	 float const Wres_50  = 2.0 * 3.1415927 * 50.0;
	 float const kt = 2.6666666e4;

	 float const a1 = 2 * kr * kt * Wdamp_50;
	 float const b0 = kt * kt + 2 * kt * Wdamp_50 + Wres_50  * Wres_50 ;
	 float const b1 = 2 * kt * kt - 2 * Wres_50  * Wres_50 ;
	 float const b2 = kt * kt + 2 * kt * Wdamp_50 + Wres_50  * Wres_50 ;

     static float E_Prev2 = 0;
     static float E_Prev1 = 0;
     static float U_Prev2 = 0;
     static float U_Prev1 = 0;

	 // Calculations for the PI controller:
	 I_OUT_PID.setpoint = LO_Sample_256 * I_Output_Demand;
	 I_OUT_PID.input = I_grid;
	 PIDCompute(&I_OUT_PID);

	 // Calculations for the resonant controller:
	 float Ua = a1 * E_Prev1 - a1 * E_Prev2;
	 float Ub = b1 * U_Prev1 - b2 * U_Prev2;
	 float Ui = (Ua + Ub) / b0;

     E_Prev2 = E_Prev1;
     E_Prev1 = I_OUT_PID.error;
     U_Prev2 = U_Prev1;
     U_Prev1 = Ui;

	 float Demanded_Output_Voltage = I_OUT_PID.output + Ui;
	 Duty_Cycle = (int16_t)(Demanded_Output_Voltage * DUTY_MAX / V_bus);			//Duty_Cycle = (int16_t)(LO_Sample_256 * 3.8);

	// Constrain and output the new duty cycle
	Duty_Cycle = CONSTRAIN(Duty_Cycle, -DUTY_LIMIT, DUTY_LIMIT);

	if(Prev_Duty_Cycle < 0 && Duty_Cycle >= 0)	{									// These stop rare glitches from occurring at the zero-crossing-points
		htim1.Instance->CNT = 0;
	}
	else if(Prev_Duty_Cycle >= 0 && Duty_Cycle < 0)	{
		htim1.Instance->CNT = 0;
	}

	int16_t Inverse_Duty_Cycle = 1000 + Duty_Cycle;
	if(Duty_Cycle >= 0) {
		htim1.Instance->CCR1 = 0;
		htim1.Instance->CCR2 = Duty_Cycle;
	}
	else {
		htim1.Instance->CCR1 = 1000;
		htim1.Instance->CCR2 = Inverse_Duty_Cycle;
	}

	Prev_Duty_Cycle = Duty_Cycle;

	/* Output to DAC for debugging */
	//uint32_t DAC_Data = 2048 + (int32_t)(Ui * 1000.0f);
	//uint32_t DAC_Data = 2048 + (int32_t)(LO_Sample_256*4.0);
	uint32_t DAC_Data = 2048 + (int32_t)(I_grid*1000.0);
	HAL_DAC_SetValue(&hdac1, DAC_CHANNEL_2, DAC_ALIGN_12B_R, DAC_Data);
}

void PLL()	{
	int32_t Signal_Multiple = (int32_t)(Cos_LookupF[_50_Index] * V_grid);			// Multiply the LO Cosine value with our current phase voltage sample
	PLL_PID.input = Integral(Signal_Multiple);   									// Integrate this Multiple over the last 1 period
	PIDCompute(&PLL_PID); 															// Plug result in a PI controller to maintain 0 phase shift

	TIM4->ARR = SINE_STEP_PERIOD;// - (int32_t)PLL_PID.output; 						// adjust LO frequency (step period) to synchronise to mains phase

	_50_Index++;  																	// Increment our LO indices
	if(_50_Index == SINE_STEPS)
		_50_Index = 0;
}

void HAL_TIM_PeriodElapsedCallback(TIM_HandleTypeDef *htim) {
	if (htim == &htim2)	{
		Run_Grid_Checks_Flag = 1;													// #### Runs every 1.25ms to perform our safety checks ####
	}

	if (htim == &htim3)	{
		Run_Controller_Flag = 1;													// ### Runs every 100us to iterate the controller ###
	}

	if (htim == &htim4)	{															// ### Runs 3.2 kHz and iterates the PLL ###
		PLL();
	}
}


/* USER CODE END 4 */
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


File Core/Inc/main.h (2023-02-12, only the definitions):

#define DFSDM_Clk_Pin GPIO_PIN_2
#define DFSDM_Clk_GPIO_Port GPIOC
#define LED_Pin GPIO_PIN_2
#define LED_GPIO_Port GPIOA
#define DAC_Out_Pin GPIO_PIN_5
#define DAC_Out_GPIO_Port GPIOA
#define Phase_BN_Pin GPIO_PIN_7
#define Phase_BN_GPIO_Port GPIOA
#define Phase_AN_Pin GPIO_PIN_0
#define Phase_AN_GPIO_Port GPIOB
#define Vbus_DIN_Pin GPIO_PIN_1
#define Vbus_DIN_GPIO_Port GPIOB
#define Igrid_DIN_Pin GPIO_PIN_12
#define Igrid_DIN_GPIO_Port GPIOB
#define Vgrid_DIN_Pin GPIO_PIN_14
#define Vgrid_DIN_GPIO_Port GPIOB
#define Icap_DIN_Pin GPIO_PIN_7
#define Icap_DIN_GPIO_Port GPIOC
#define Phase_B_Pin GPIO_PIN_8
#define Phase_B_GPIO_Port GPIOA
#define Phase_A_Pin GPIO_PIN_9
#define Phase_A_GPIO_Port GPIOA
#define Relay_Pin GPIO_PIN_11
#define Relay_GPIO_Port GPIOA

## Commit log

2022-12-27 Not yet finished PCB
    Nearly finished. Just checking, double checking and triple checking all pins, chips and connections.
    [GTI_V4_KiCad.kicad_pcb, GTI_V4_KiCad.kicad_sch, GTI_V4_KiCad.sch]
2023-01-01 99% finished PCB
    [GTI_V4_KiCad.kicad_pcb, GTI_V4_KiCad.kicad_sch]
2023-01-01 Completed PCB - sent for fabrication
    Sent to PCBWay for fabrication
    [GTI_V4_KiCad.kicad_pcb]
2023-02-16 Uploaded BOM
    [GTI_v4_BOM.csv]
2023-02-16 The finished and used PCB
    [GTI_V4_KiCad.kicad_sch]
2023-02-16 Finished and used Schematic and PCB
    [GTI_V4_KiCad.kicad_pcb, GTI_V4_KiCad.kicad_sch, GTI_V4_KiCad.sch]
2023-03-15 update BOM - to add XO part number and link
    [GTI_v4_BOM.csv]

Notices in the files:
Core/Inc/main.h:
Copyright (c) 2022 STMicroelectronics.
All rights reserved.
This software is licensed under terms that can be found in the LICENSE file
